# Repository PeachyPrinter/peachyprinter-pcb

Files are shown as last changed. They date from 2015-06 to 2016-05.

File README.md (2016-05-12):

If you're looking for the version of the Peachy Printer that we were gearing up to manufacture, look at mini-v1.14. 

If you're wondering what v1.15 is all about, it's a work-in-progress that we started because of a huge panic: right around the time we were getting ready for our final test manufacturing run, the STM32F042 practically vanished from the entire supply chain! We couldn't find them anywhere! So I quickly started redoing the board to use an STM32F070 instead, but in the end the supply chain recovered before we had to pull the trigger on the respin.

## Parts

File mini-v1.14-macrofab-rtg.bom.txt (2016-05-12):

Partlist exported from C:/Users/Tony/Dropbox/eagle/Peachy Pro/mini-v1.14-macrofab-rtg.sch at 2015-11-02 10:18 AM

Qty Value                Device                 Package           Parts                                                                    Description                                          MFG# MPN                           TEMP_COF TOLERANCE TP_SIGNAL_NAME VOLTAGE WATTAGE
4                        LEDCHIP-LED0603        CHIP-LED0603      LED1, LED2, LED3, LED4                                                   LED                                                                                                                                      
1                        PINHD-1X2              1X02              JP4                                                                      PIN HEADER                                                                                                                               
3                        PINHD-2X3              2X03              JP3, JP5, JP6                                                            PIN HEADER                                                                                                                               
1                        USB_MICRO_RIGHT        MICROUSB-RIGHT    J1                                                                       Library:  MF_Connectors                                                                                                                  
4   0.1uF                C-USC0603              C0603             C10, C11, C12, C13                                                       CAPACITOR, American symbol                                                                                                               
5   0.1uF                CAPACITOR_NP_0603      C0603             C8, C14, C16, C18, C20                                                   Library:  MF_Passives                                N/A                                N/A      N/A                      N/A            
2   10                   RESISTOR_0603          R0603             R16, R25                                                                 Library:  MF_Passives                                N/A                                         N/A                      N/A     N/A    
1   100k                 RESISTOR_0603          R0603             R4                                                                       Library:  MF_Passives                                N/A                                         N/A                      N/A     N/A    
4   100n                 CAPACITOR_NP_0603      C0603             C4, C5, C6, C7                                                           Library:  MF_Passives                                N/A                                N/A      N/A                      N/A            
1   10uF                 CAPACITOR_P_4MM        CP4MM             C3                                                                       Library:  MF_Passives                                N/A                                         N/A                      N/A            
2   13k3                 RESISTOR_0603          R0603             R1, R18                                                                  Library:  MF_Passives                                N/A                                         N/A                      N/A     N/A    
5   1k69                 RESISTOR_0603          R0603             R13, R14, R15, R38, R43                                                  Library:  MF_Passives                                N/A                                         N/A                      N/A     N/A    
2   1uF                  C-USC0603              C0603             C1, C2                                                                   CAPACITOR, American symbol                                                                                                               
3   1uF                  CAPACITOR_NP_0603      C0603             C9, C17, C19                                                             Library:  MF_Passives                                N/A                                N/A      N/A                      N/A            
16  2k                   RESISTOR_0603          R0603             R2, R3, R5, R7, R8, R9, R10, R20, R21, R22, R23, R27, R28, R29, R36, R37 Library:  MF_Passives                                N/A                                         N/A                      N/A     N/A    
1   560pF/50V            C-USC0603              C0603             C15                                                                      CAPACITOR, American symbol                                                                                                               
5   604k                 RESISTOR_0603          R0603             R24, R26, R32, R34, R41                                                  Library:  MF_Passives                                N/A                                         N/A                      N/A     N/A    
1   63k4                 RESISTOR_0603          R0603             R17                                                                      Library:  MF_Passives                                N/A                                         N/A                      N/A     N/A    
10  825k                 RESISTOR_0603          R0603             R6, R11, R12, R19, R30, R31, R33, R35, R39, R40                          Library:  MF_Passives                                N/A                                         N/A                      N/A     N/A    
1   BAT42                DIODE_SOD-123          SOD-123           D1                                                                       Library:  MF_Discrete_Semiconductor                  N/A                                                                                 
2   BSS138               N-CHANNEL_FET_SOT-23-3 SOT-23-3          U1, U3                                                                   Library:  MF_Discrete_Semiconductor                                                                                                      
1   GND                  TPB2,54                B2,54             TP2                                                                      Test pad                                                                                                                                 
4   LMC7101              LMC7101                SOT23-5           U$7, U$15, U$16, U$17                                                                                                                                                                                             
1   LMC7101              OPAMP-SINGLELMC7101    SOT23-5           U$5                                                                      Single amp opamps                                                                                                                        
1   LMR62014             LMR62014               SOT23-5           U$8                                                                                                                                                                                                               
1   MBR0520              MBR0520                SOD123            U$9                                                                                                                                                                                                               
1   N/C                  RESISTOR_0603          R0603             R42                                                                      Library:  MF_Passives                                N/A                                         N/A                      N/A     N/A    
2   NC7WZ14P6X           NC7WZ14P6X             SC70-6            U$2, U$4                                                                 2-circuit logic inverter, ultra-high-speed and cheap                                                                                     
1   SCOTT_LASERDIODELD3  SCOTT_LASERDIODELD3    SCOTT_LASERDIODE3 LD1                                                                                                                                3 x (0552-2-15-15-11-27-10-0)                                                  
1   SDR0403-100ML        SDR0403                SDR0403           U$14                                                                                                                                                                                                              
2   SMF6.0A              MBR0520                SOD123            U$10, U$13                                                                                                                                                                                                        
1   SP3002-04JTG         SP3002                 SC70-6            U$12                                                                                                                                                                                                              
1   STM32F042C6T6-LQFP48 STM32F042-LQFP48       LQFP48            U$1                                                                                                                                                                                                               
1   TLV70233PDBVR        TLV70233PDBVR          SOT-23-5          U2                                                                       Manufacturer Part #: TLV702                                                                                                              
10  TPB1,27              TPB1,27                B1,27             3V, GND, NRST, SWCLK, SWDIO, TP3, TP4, TP5, TP6, VUSB                    Test pad                                                                                                                                 
1   TPB2,54              TPB2,54                B2,54             LASER                                                                    Test pad                                                                                                                                 
1   ferrite              L-US                   C0603             L1                                                                       INDUCTOR, American symbol

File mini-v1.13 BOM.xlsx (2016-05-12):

Part | MF Part
2x3 Header | MF-CON-2.54mm-2x3 (https://beta.macrofab.net/project/9qdpte)
1u 0603 | MF-CAP-0603-1uF (https://beta.macrofab.net/part/MF-CAP-0603-1uF)
0.1u 0603 | MF-CAP-0603-0.1uF (https://beta.macrofab.net/part/MF-CAP-0603-0.1uF)
560pF | 399-1076-1-ND
ferrite | 445-1565-1-ND
LED | MF-LED-0603-RED
10u 4mm | MF-CAP-4MM-10uF (https://beta.macrofab.net/project/5xndt7)
2k | MF-RES-0603-2K (https://beta.macrofab.net/project/9qdpte/3)
825k | MF-RES-0603-825K (https://beta.macrofab.net/project/9qdpte/4)
1.69k | MF-RES-0603-1.69K (https://beta.macrofab.net/project/9qdpte/3)
63k4 | CRCW060363K4FKEA (https://beta.macrofab.net/project/9qdpte/3)
604k | MF-RES-0603-604K
13k3 | CRCW060313K3FKEA (https://beta.macrofab.net/project/9qdpte/3)
MBR0520 | MBR0520LCT-ND
mosfet | MF-DSC-SOT233-BSS138 (https://beta.macrofab.net/part/MF-DSC-SOT233-BSS138)
ldo | MF-SOT-235-3.3V-300mA (https://beta.macrofab.net/part/MF-SOT-235-3.3V-300mA)
lmc7101 | 576-2575-1-ND
lmr62014 | LMR62014XMF/NOPBCT-ND

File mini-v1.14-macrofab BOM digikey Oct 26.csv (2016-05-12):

Qty | Value | Device | DK P/N | Extended | DK for Ext$ | Package | DK Order Oct 26 | Boards Oct 26
13 | 100n | CAPACITOR_NP_0603 | 399-1095-2-ND | 65000 | 362.7 | C0603 | 4000 | 307
1 | 10uF | CAPACITOR_P_4MM | 490-7201-2-ND | 5000 | 484.35 | CP4MM | 250 | 250
5 | 1uF | C-USC0603 | 311-1443-2-ND | 25000 | 178.25 | C0603 | 4000 | 800
1 | 560pF/50V | C-USC0603 | 1276-1278-2-ND | 5000 | 62.9 | C0603 | 4000 | 4000
1 | BAT42 | DIODE_SOD-123 | BAT42W-FDITR-ND | 5000 | 442.2 | SOD-123 | 120 | 120
4 |  | LEDCHIP-LED0603 | 475-2512-2-ND | 20000 | 1071.2 | CHIP-LED0603 | 1000 | 250
5 | LMC7101 | LMC7101 | 576-2575-2-ND | 25000 | 7725.5 | SOT23-5 | 600 | 120
1 | LMR62014 | LMR62014 | 296-39046-2-ND | 5000 | 2595.55 | SOT23-5 | 120 | 120
1 | ferrite | L-US |  | 5000 |  | C0603 |  | 0
1 | MBR0520 | MBR0520 | MBR0520LT1GOSTR-ND | 5000 | 397.2 | SOD123 | 120 | 120
2 | SMF6.0A | MBR0520 | F5749TR-ND | 10000 | 1517.1 | SOD123 | 250 | 125
2 | NC7WZ14P6X | NC7WZ14P6X | NC7WZ14P6XTR-ND | 10000 | 810.4 | SC70-6 | 250 | 125
2 | BSS138 | N-CHANNEL_FET_SOT-23-3 | BSS138LT3GOSTR-ND | 10000 | 451.64 | SOT-23-3 | 240 | 120
3 |  | PINHD-2X3 | 952-1921-ND | 15000 | 2617.5 | 2X03 | 360 | 120
2 | 10 | RESISTOR_0603 | 311-10.0HRTR-ND | 10000 | 21.26 | R0603 | 5000 | 2500
1 | 100k | RESISTOR_0603 | 311-100KHRTR-ND | 5000 | 9.62 | R0603 | 5000 | 5000
2 | 13k3 | RESISTOR_0603 | 311-13.3KHRTR-ND | 10000 | 21.26 | R0603 | 5000 | 2500
5 | 1k69 | RESISTOR_0603 | 311-1.69KHRTR-ND | 25000 | 47.5 | R0603 | 5000 | 1000
16 | 2k | RESISTOR_0603 | 311-2.00KHRTR-ND | 80000 | 139.2 | R0603 | 5000 | 312
5 | 604k | RESISTOR_0603 | 311-604KHRTR-ND | 25000 | 47.5 | R0603 | 5000 | 1000
1 | 63k4 | RESISTOR_0603 | 311-63.4KHRTR-ND | 5000 | 12.45 | R0603 | 5000 | 5000
10 | 825k | RESISTOR_0603 | 311-825KHRTR-ND | 50000 | 21.62 | R0603 | 5000 | 500
1 | SDR0403-100ML | SDR0403 | SDR0403-100MLTR-ND | 5000 | 1287.25 | SDR0403 | 120 | 120
1 | SP3002-04JTG | SP3002 | F2916TR-ND | 5000 | 1824.75 | SC70-6 | 120 | 120
1 | STM32F070CBT6 | STM32F042-LQFP48 | 497-15099-ND | 5000 | 8179.93 | LQFP48 | 120 | 120
1 | TLV70233PDBVR | TLV70233PDBVR | 296-39284-2-ND | 5000 | 767.64 | SOT-23-5 | 120 | 120
1 |  | USB_MICRO_RIGHT | 609-4618-2-ND | 5000 | 1258.45 | MICROUSB-RIGHT | 120 | 120
TOTAL |  |  |  |  | 32354.92
PER BOARD |  |  |  |  | 6.470984

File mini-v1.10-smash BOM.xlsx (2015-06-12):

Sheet: mini-v1.10-smash
Qty | Total Qty | Value | Device | Package | Digikey Part
1 | 15 | 10uF | C-USC0603 | C0603 | 490-10475-1-ND |  | Number of Boards | 15
1 | 15 | 560pF/50V | C-USC0603 | C0603 | 399-1076-1-ND |  | Breakage | 0%
1 | 15 | 2.2u | C-USC0603 | C0603 | 587-2983-1-ND
1 | 15 | 10n | C-USC0603 | C0603 | 399-1091-1-ND
1 | 15 | 470p | C-USC0603 | C0603 | 399-1075-1-ND
1 | 15 | 820n | C-USC0603 | C0603 | 399-3117-1-ND
1 | 15 | 74S04D | 74S04D | SO14 | 568-1384-1-ND
1 | 15 | ferrite | L-US | C0603 | 445-1565-1-ND
1 | 15 | IRLR3105TR | FET-N-IRLR3105TRIRLR3105TR | DPAK | IRLR3105TRPBFCT-ND
1 | 15 | 10k | R-US_R0603 | R0603 | 541-10.0KHCT-ND
1 | 15 | 1 | R-US_R0603 | R0603 | 541-1.00HHCT-ND
1 | 15 | 100 | R-US_R0603 | R0603 | 541-100HCT-ND
1 | 15 | 9k9 | R-US_R0603 | R0603 | 541-9.09KHCT-ND
1 | 15 | 52k3 | R-US_R0603 | R0603 | 541-52.3KHCT-ND
1 | 15 | 13k3 | R-US_R0603 | R0603 | 541-13.3KHCT-ND
1 | 15 | 100k | R-US_R0603 | R0603 | 541-100KHCT-ND
1 | 15 | LD3985M33R | LD3985MXXR | SOT23-5L | LP3985IM5-3.3/NOPBCT-ND
1 | 15 | STM32F042-LQFP48 | STM32F042-LQFP48 | LQFP48 | 497-14648-ND
1 | 15 | SDR0403-100ML | SDR0403 | SDR0403 | SDR0403-100MLCT-ND
1 | 15 | FCI-MICRO-USB | FCI-MICRO-USB | FCI-MICROUSB | 609-4613-1-ND
1 | 15 | LMR62014 | LMR62014 | SOT23-5 | LMR62014XMF/NOPBCT-ND
1 | 15 | MBR0520 | MBR0520 | SOD123 | MBR0520LCT-ND
1 | 15 | LMH6645MF | OPAMP-SINGLELMH6645MF | SOT23-5 | LMH6645MF/NOPBCT-ND
2 | 30 | BAT60A | BAT60A | SOD323 | BAT60AE6327INCT-ND
2 | 30 | SMF6.0A | MBR0520 | SOD123 | F5749CT-ND
2 | 30 | SP3002 | SP3002 | SC70-6 | F2916CT-ND | Substituted
3 | 45 | 1u | C-USC0603 | C0603 | 587-1242-1-ND
4 | 60 | 470n | C-USC0603 | C0603 | 587-1252-1-ND
4 | 60 | 4.7n | C-USC0603 | C0603 | 399-1087-1-ND
4 | 60 |  | LEDCHIP-LED0603 | CHIP-LED0603 | 475-2512-1-ND
4 | 60 | LMC7101 | LMC7101 | SOT23-5 | 576-2575-1-ND
5 | 75 | 100n | C-USC0603 | C0603 | 399-1095-1-ND
5 | 75 | 1M | R-US_R0603 | R0603 | 541-1.00MHCT-ND
6 | 90 | 1k | R-US_R0603 | R0603 | 541-1.00KHCT-ND
12 | 180 | 1k96 | R-US_R0603 | R0603 | 541-1.96KHCT-ND

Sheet: Digikey Kitting
#Kits | Cost | Cost/Board
1 | 40 | 40
15 | 338.33 | 22.55533333
20 | 440 | 22
1000 | 10118.43 | 10.11843
2500 | 27284.62 | 10.913848
5000 | 47519.85 | 9.50397

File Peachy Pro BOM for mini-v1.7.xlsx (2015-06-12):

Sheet: Ordering
Value | Device | Package | Digikey Part | Newark Part Number | Unit Price | /1000 price | QTY | Single Price | Vol Price | QTY +15%
100n | C-USC0603 | C0603 | 399-1095-1-ND |  | 0.13 | 0.00816 | 5 | 0.65 | 0.0408 | 58
10n | C-USC0603 | C0603 | 399-8988-1-ND |  | 0.32 | 0.06934 | 1 | 0.32 | 0.06934 | 12
10uF | C-USC0603 | C0603 | 490-10475-1-ND |  | 0.27 | 0.05056 | 1 | 0.27 | 0.05056 | 12
1u | C-USC0603 | C0603 | 587-1242-1-ND |  | 0.13 | 0.01321 | 3 | 0.39 | 0.03963 | 35
2.2u | C-USC0603 | C0603 | 587-2983-1-ND |  | 0.22 | 0.04095 | 1 | 0.22 | 0.04095 | 12
4.7n | C-USC0603 | C0603 | 399-1087-1-ND |  | 0.13 | 0.00971 | 4 | 0.52 | 0.03884 | 46
470n | C-USC0603 | C0603 | 587-1252-1-ND |  | 0.13 | 0.02136 | 4 | 0.52 | 0.08544 | 46
470p | C-USC0603 | C0603 | 399-1075-1-ND |  | 0.13 | 0.01398 | 1 | 0.13 | 0.01398 | 12
560pF/50V | C-USC0603 | C0603 | 399-1076-1-ND |  | 0.32 | 0.07911 | 1 | 0.32 | 0.07911 | 12
820n | C-USC0603 | C0603 | 399-3117-1-ND |  | 0.34 | 0.08216 | 1 | 0.34 | 0.08216 | 12
BAT60A | BAT60A | SOD323 | BAT60AE6327INCT-ND |  | 0.71 | 0.14888 | 2 | 1.42 | 0.29776 | 23
74S04D | 74S04D | SO14 | 568-1384-1-ND |  | 0.63 | 0.13336 | 1 | 0.63 | 0.13336 | 12
 | LEDCHIP-LED0603 | CHIP-LED0603 | 475-2512-1-ND |  | 0.12 | 0.06086 | 4 | 0.48 | 0.24344 | 46
IRLR3105TR | FET-N-IRLR3105TRIRLR3105TR | DPAK | IRLR3105TRPBFCT-ND |  | 1.48 | 0.5535 | 1 | 1.48 | 0.5535 | 12
1 | R-US_R0603 | R0603 | 541-1.00HHCT-ND |  | 0.112 | 0.02359 | 1 | 0.112 | 0.02359 | 12
100 | R-US_R0603 | R0603 | 541-100HCT-ND |  | 0.112 | 0.02359 | 1 | 0.112 | 0.02359 | 12
100k | R-US_R0603 | R0603 | 541-100KHCT-ND |  | 0.112 | 0.02359 | 1 | 0.112 | 0.02359 | 12
10k | R-US_R0603 | R0603 | 541-10.0KHCT-ND |  | 0.112 | 0.02359 | 1 | 0.112 | 0.02359 | 12
13k3 | R-US_R0603 | R0603 | 541-13.3KHCT-ND |  | 0.112 | 0.02359 | 1 | 0.112 | 0.02359 | 12
1k | R-US_R0603 | R0603 | 541-1.00KHCT-ND |  | 0.112 | 0.02359 | 2 | 0.224 | 0.04718 | 23
1M | R-US_R0603 | R0603 | 541-1.00MHCT-ND |  | 0.112 | 0.02359 | 5 | 0.56 | 0.11795 | 58
3k9 | R-US_R0603 | R0603 | 541-3.90KHCT-ND |  | 0.112 | 0.02359 | 4 | 0.448 | 0.09436 | 46
52k3 | R-US_R0603 | R0603 | 541-52.3KHCT-ND |  | 0.112 | 0.02359 | 1 | 0.112 | 0.02359 | 12
9k9 | R-US_R0603 | R0603 | 541-9.09KHCT-N |  | 0.112 | 0.02359 | 1 | 0.112 | 0.02359 | 12
LD3985M33R | LD3985MXXR | SOT23-5L | 497-3504-1-ND |  | 0.96 | 0.33535 | 1 | 0.96 | 0.33535 | 12
 | R-US_R0603 | R0603 | 541-1.00KHCT-ND |  | 0.112 | 0.02359 | 4 | 0.448 | 0.09436 | 46
FCI-MICRO-USB | FCI-MICRO-USB | FCI-MICROUSB | 609-4613-1-ND |  | 0.6 | 0.3365 | 1 | 0.6 | 0.3365 | 12
LMC7101 | LMC7101 | SOT23-5 | 576-2575-1-ND |  | 0.98 | 0.389 | 4 | 3.92 | 1.556 | 46
LMH6645MF | OPAMP-SINGLELMH6645MF | SOT23-5 | LMH6645MF/NOPBCT-ND |  | 2.49 | 0.97596 | 1 | 2.49 | 0.97596 | 12
LMR62014 | LMR62014 | SOT23-5 | LMR62014XMF/NOPBCT-ND |  | 2.32 | 0.80116 | 1 | 2.32 | 0.80116 | 12
MBR0520 | MBR0520 | SOD123 | MBR0520LT1GOSCT-ND | 48K7498 | 0.407 | 0.076 | 3 | 1.221 | 0.228 | 35
SDR0403-100ML | SDR0403 | SDR0403 | SDR0403-100MLCT-ND |  | 0.65 | 0.31547 | 1 | 0.65 | 0.31547 | 12
SP3002 | SP3002 | SC70-6 | F2916CT-ND |  | 0.96 | 0.38456 | 2 | 1.92 | 0.76912 | 23
STM32F042-LQFP48 | STM32F042-LQFP48 | LQFP48 | 497-14648-ND |  | 4.08 | 2.04112 | 1 | 4.08 | 2.04112 | 12
 | L_TDK_1005 | MLK1005 | 445-1565-1-ND |  | 0.13 | 0.03518 | 1 | 0.13 | 0.03518 | 12
 | NOTE: Replace the existing one with this one (0603)
 |  |  |  |  |  |  | 68 | 28.445 | 9.68171

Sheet: Assembly
Value | QTY | x3
100n | 5 | 15
10n | 1 | 3
10uF | 1 | 3
1u | 3 | 9
2.2u | 1 | 3
4.7n | 4 | 12
470n | 4 | 12
470p | 1 | 3
560pF/50V | 1 | 3
820n | 1 | 3
BAT60A | 2 | 6
74S04D | 1 | 3
 | 4 | 12
IRLR3105TR | 1 | 3
1 | 1 | 3
100 | 1 | 3
100k | 1 | 3
10k | 1 | 3
13k3 | 1 | 3
1k | 2 | 6
1M | 5 | 15
3k9 | 4 | 12
52k3 | 1 | 3
9k9 | 1 | 3
LD3985M33R | 1 | 3
 | 4 | 12
FCI-MICRO-USB | 1 | 3
LMC7101 | 4 | 12
LMH6645MF | 1 | 3
LMR62014 | 1 | 3
MBR0520 | 3 | 9
SDR0403-100ML | 1 | 3
SP3002 | 2 | 6
STM32F042-LQFP48 | 1 | 3
 | 1
 | 68

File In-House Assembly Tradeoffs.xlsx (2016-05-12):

Item | Cost ($USD) | Cost ($CAD) | Assumptions/Notes
Pick and Place Machine |  | $17415.00 | Probably need extra feeders (DP2006-3)
Labour |  | $4933.33 | 1hr per batch labour, 75 boards per batch, $20/hr + 1 week setup time @ $90/hr
Components |  | $32354.92
PCB Manufacture |  | 5148.60 | RFQ from goldphoenix for 5000 boards, 11 day lead
Total |  | $59851.85
Components | $27850.00 | $37597.50 | 1.35 exchange rate
PCBs | $2150.00 | $2902.50
Labour | $13400.00 | $18090.00
Total |  | $58590.00 | or $60,702 to do it in 2 batches of 2500

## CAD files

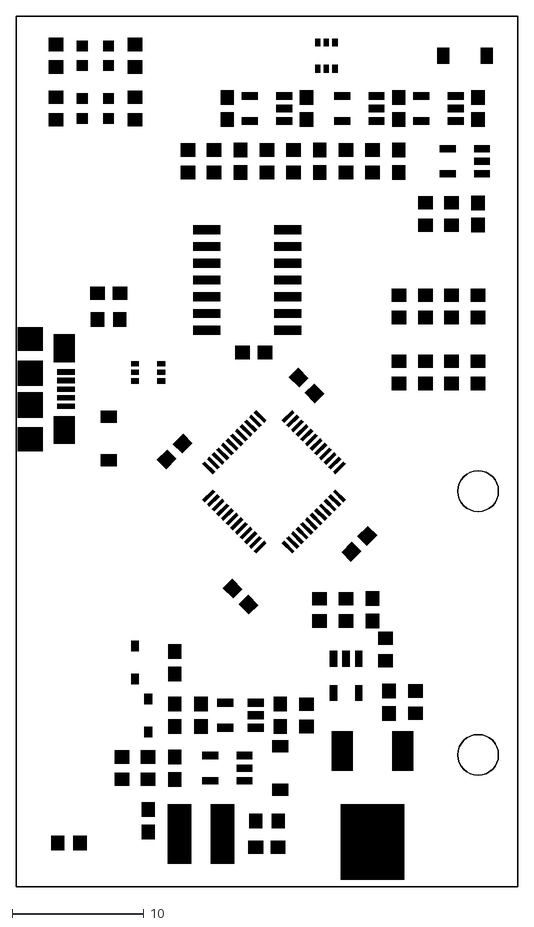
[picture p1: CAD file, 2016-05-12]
mini-v1.10-smash-4.dxf
38.0 x 66.0

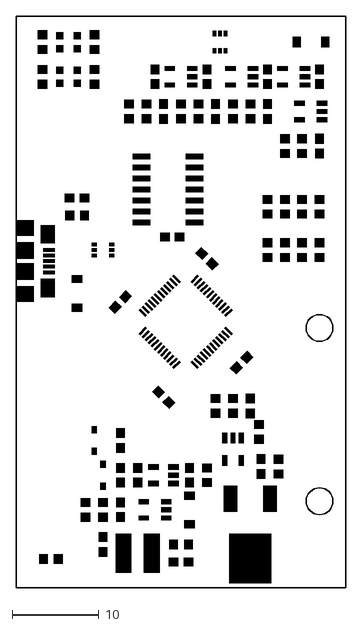
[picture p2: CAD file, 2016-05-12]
mini-v1.10-smash-3.dxf
38.0 x 66.0

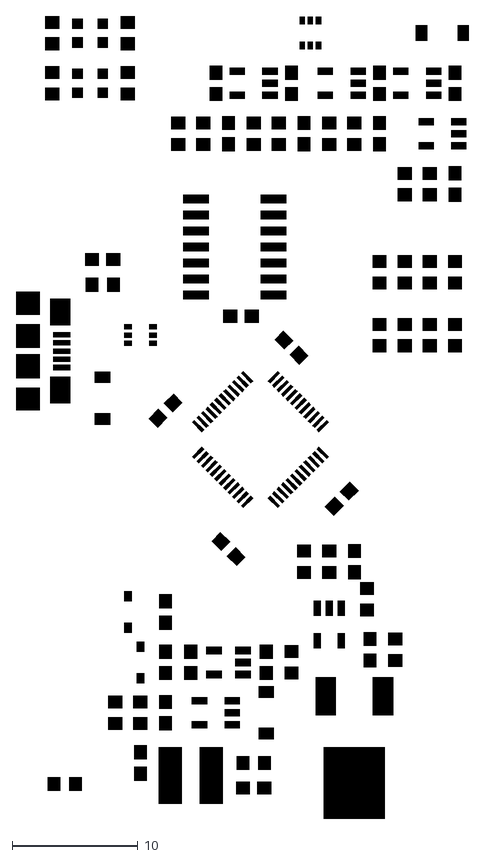
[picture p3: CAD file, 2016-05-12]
mini-v1.10-smash-7.dxf
36.0 x 63.8

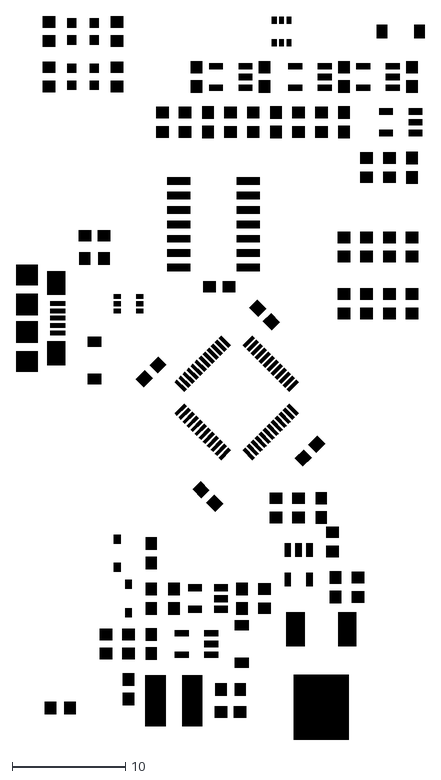
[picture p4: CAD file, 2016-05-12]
mini-v1.10-smash-10.dxf
36.0 x 63.8

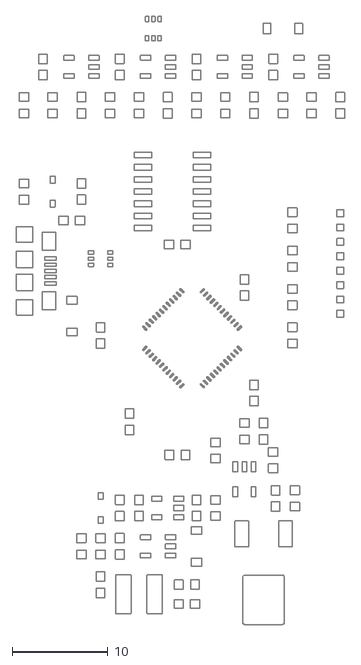
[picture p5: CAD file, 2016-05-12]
mini-v1.7-bigger-tcream-tweaked.dxf
34.2 x 63.4

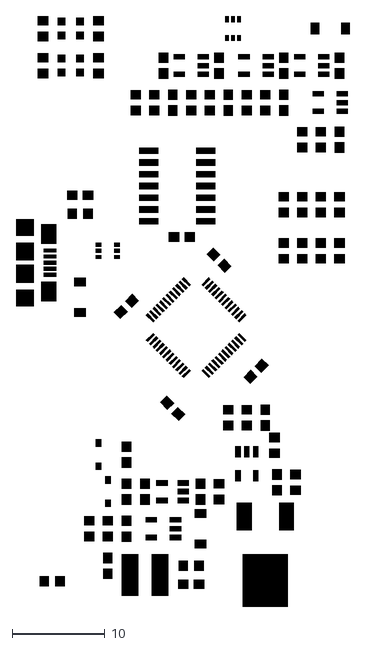
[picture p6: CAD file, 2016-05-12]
mini-v1.10-smash-6.dxf
36.0 x 63.8

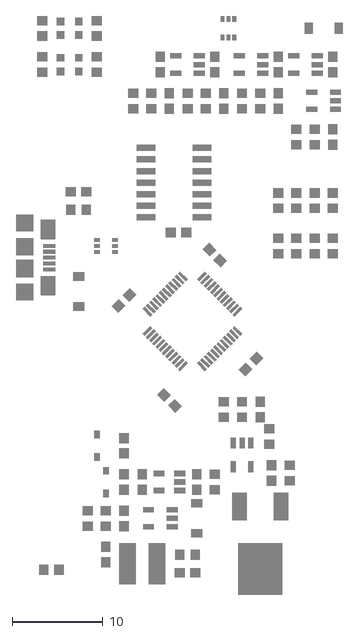
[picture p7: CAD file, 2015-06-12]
mini-v1.10-smash-8.dxf
36.0 x 63.8

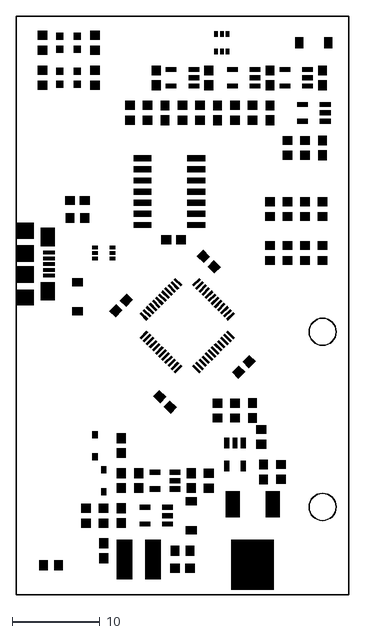
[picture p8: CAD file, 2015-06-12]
mini-v1.10-smash-2.dxf
38.0 x 66.0

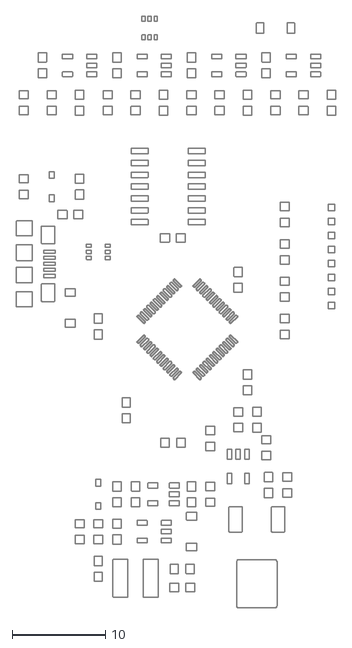
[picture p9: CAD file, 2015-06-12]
mini-v1.7-bigger-tcream.dxf
34.2 x 63.4

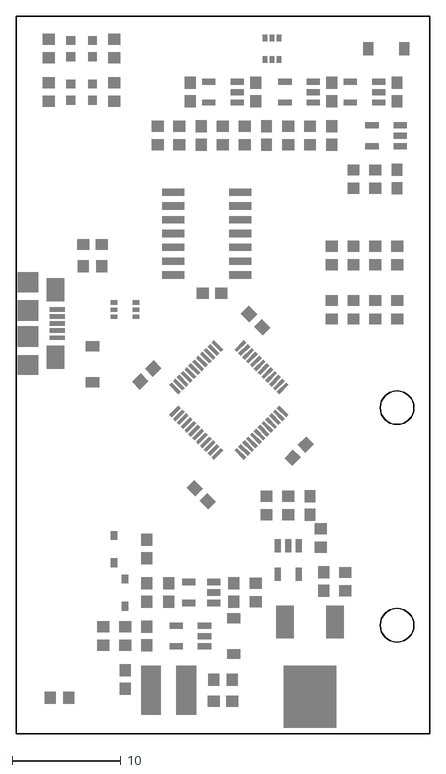
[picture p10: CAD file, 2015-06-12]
mini-v1.10-smash-5.dxf
38.0 x 66.0

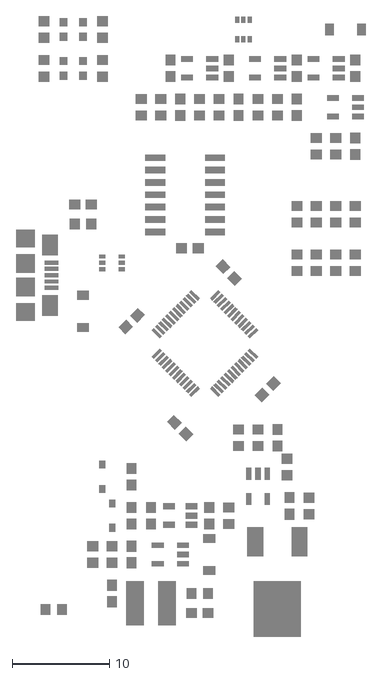
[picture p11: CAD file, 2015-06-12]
mini-v1.10-smash-9.dxf
36.0 x 63.8

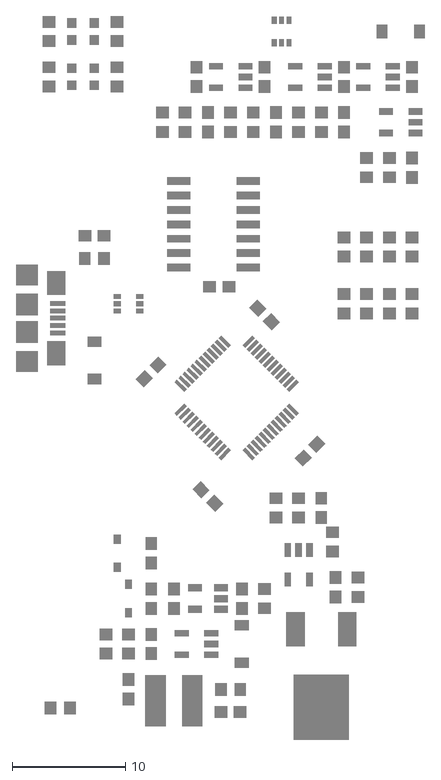
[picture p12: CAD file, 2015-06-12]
mini-v1.10-smash-7.1.dxf
36.0 x 63.8

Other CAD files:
mini-v1.10-smash-bcream.dxf
mini-v1.10-smash-tcream.dxf
mini-v1.10-smash-10.dwg
mini-v1.10-smash.dwg

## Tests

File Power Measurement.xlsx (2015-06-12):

Power Setting | Approx Current (mA) | Raw Measurement uW | Corrected mW | Raw w/o aperature mW | mW w/o aperature | aperature % | Raw w/o aperature, bigger dot | mW w/o aperature, bigger | Big dot/small
12 | 15.52941176 |  |  |  |  |  | 0.00361 | 0.035017 |  | Note: this was all done with a 10:1 current setting ratio. Iout = 3.3V * 1/10 (A/V) * x / 255 This is both dangerous and inefficient. We're going to change the ratio s.t. ~25mW output power is represented by 255. This would have been on v1.7 of the circuit
15 | 19.41176471 |  |  |  |  |  | 0.00467 | 0.045299
19 | 24.58823529 |  |  |  |  |  | 0.00682 | 0.066154
20 | 25.88235294 |  |  |  |  |  | 0.00768 | 0.074496
25 | 32.35294118 |  |  | 0.085 | 0.8245 |  | 0.104 | 1.0088 | 1.223529412
30 | 38.82352941 | 78.5 | 0.76145 | 0.695 | 6.7415 | 0.1129496403 | 0.755 | 7.3235 | 1.086330935
32 | 41.41176471 | 101.6 | 0.98552 | 1.024 | 9.9328 | 0.09921875 | 1.031 | 10.0007 | 1.006835938
34 | 44 | 125.1 | 1.21347 | 1.285 | 12.4645 | 0.0973540856 | 1.306 | 12.6682 | 1.016342412
36 | 46.58823529 | 145.2 | 1.40844 | 1.541 | 14.9477 | 0.09422452953 | 1.582 | 15.3454 | 1.0266061
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

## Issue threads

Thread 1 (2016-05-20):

Missing components model codes on

luckcolors, 2016-05-20:
Hello.
I was looking at the mini-v1.14-macrofab-rtg.sch and some components names are missing(i mean the part code ):
-laser
-motor

Also it would be great if you could provide description (or name) of what goes on the following pins:

Schematic sheet 2:
-TP3
-TP4
-TP5
-TP6

Schematic sheet 3:
-TP2

Schematic sheet 4:
-3V  VUSB
-SWCLK  NRST
-SWDIO GND
Thanks in advance. :+1:

tonyarkles, 2016-05-20:
TPs are test points. 3V is the 3V rail, VUSB is the USB rail.
SWCLK/SWDIO/NRST/GND are the standard ARM Cortex-M SWD debugging
connections (similar to JTAG, but fewer wires).

No parts to be mounted for any of these.

On Fri, May 20, 2016 at 1:15 PM, luckcolors <notifications@github.com>
wrote:

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

luckcolors, 2016-05-20:
Ok thanks @tonyarkles.
Then the only thing that's really missing is the motor and laser component code.

tonyarkles, 2016-05-21:
Motor? There is no motor... Are you looking at the ferrite bead maybe?

I have no clue what the laser part number is. @Rylan?

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

luckcolors, 2016-05-21:
Ah yeah. Sorry it hough there was a motor there. :P
So then what's really missing is the laser.

luckcolors, 2016-05-21:
Also resistance value for R42 is missing.

tonyarkles, 2016-05-21:
I'm doing some yard work, but if I recall R42 was an escape hatch in case the modification between v1.13 and v1.14 didn't work. I think it's a no-place but I'll double check when I'm back inside.

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

luckcolors, 2016-05-23:
so any idea on the laser?
For sure it's ultraviolet but with what potency and Voltage would it be?

luckcolors, 2016-05-24:
The only thing i found in the sch file is the value attached to the LD1 component.
mpn 3 x (0552-2-15-15-11-27-10-0)
Which appears to be this: [http://www.digikey.com/product-detail/en/mill-max-manufacturing-corp/0552-2-15-15-11-27-10-0/ED90096-ND/947104](link).
It's a pin socket.....

tonyarkles, 2016-05-24:
Totally a placeholder. That's a carry-over from the original analog board.
We were using a socket on the boards, and then a laser diode, but I wasn't
responsible for those as far as I recall.

In general, any UV laser diode will work, so long as Vf <= around 6V, and
If is less than about 200mA. The circuit is pretty robust against different
diode parameters. It's a constant current driver, so you tell it (through
the firmware) how much current you want to go through the diode, and it
adjusts everything to make sure that much current is running through the
laser.

On Tue, May 24, 2016 at 3:41 PM, luckcolors <notifications@github.com>
wrote:

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

luckcolors, 2016-05-25:
Ok. So one last detail: must the laser light wavelenght be atleast less than 380nm(ultrviolet light boundary) or it can be more (like 405nm which is violet light check wikipedia ultraviolet for more info).

tonyarkles, 2016-05-25:
I'm pretty sure 405 is A-OK.

The socket was an LD254-3P-24 from jccherry.com.
http://jccherry.com/products/Laser_Diode_Sockets/Laser_Diode_Socket_2.54mm_pitch.pdf#view=fitV,
100

You don't *have* to use a socket, but the laser diodes are pretty sensitive
and tricky to solder without cooking it. I'm pretty sure but not 100% sure
that these sockets will work too if jccherry doesn't want to sell one-offs:
http://www.aixiz.com/store/product_info.php/cPath/70/products_id/454/osCsid/c2d8dafd1f5eaab5671f0e8ee4d64784

You can probably also find an appropriate diode from aixiz

On Wed, May 25, 2016 at 3:05 AM, luckcolors <notifications@github.com>
wrote:

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

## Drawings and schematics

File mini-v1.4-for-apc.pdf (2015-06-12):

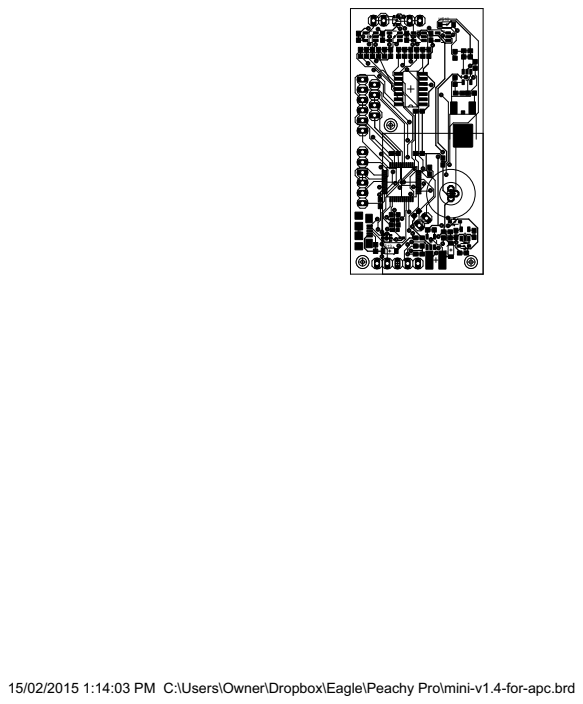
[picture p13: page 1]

15/02/2015 1:14:03 PM C:\Users\Owner\Dropbox\Eagle\Peachy Pro\mini-v1.4-for-apc.brd

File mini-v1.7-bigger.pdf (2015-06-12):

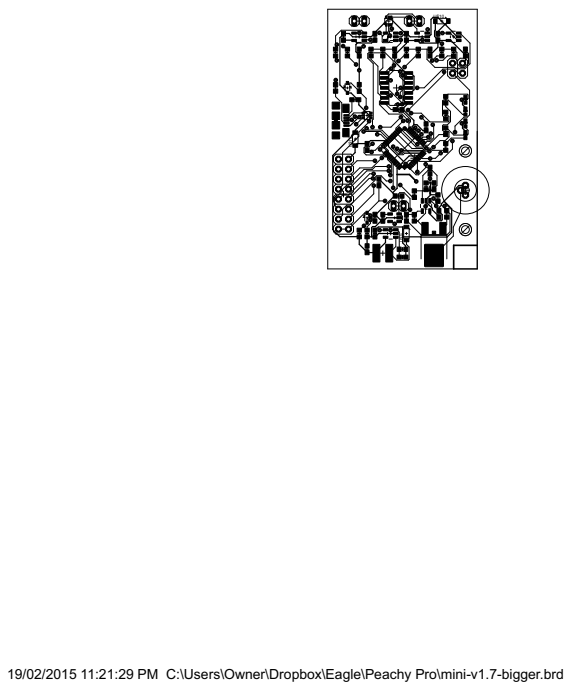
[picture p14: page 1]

19/02/2015 11:21:29 PM C:\Users\Owner\Dropbox\Eagle\Peachy Pro\mini-v1.7-bigger.brd

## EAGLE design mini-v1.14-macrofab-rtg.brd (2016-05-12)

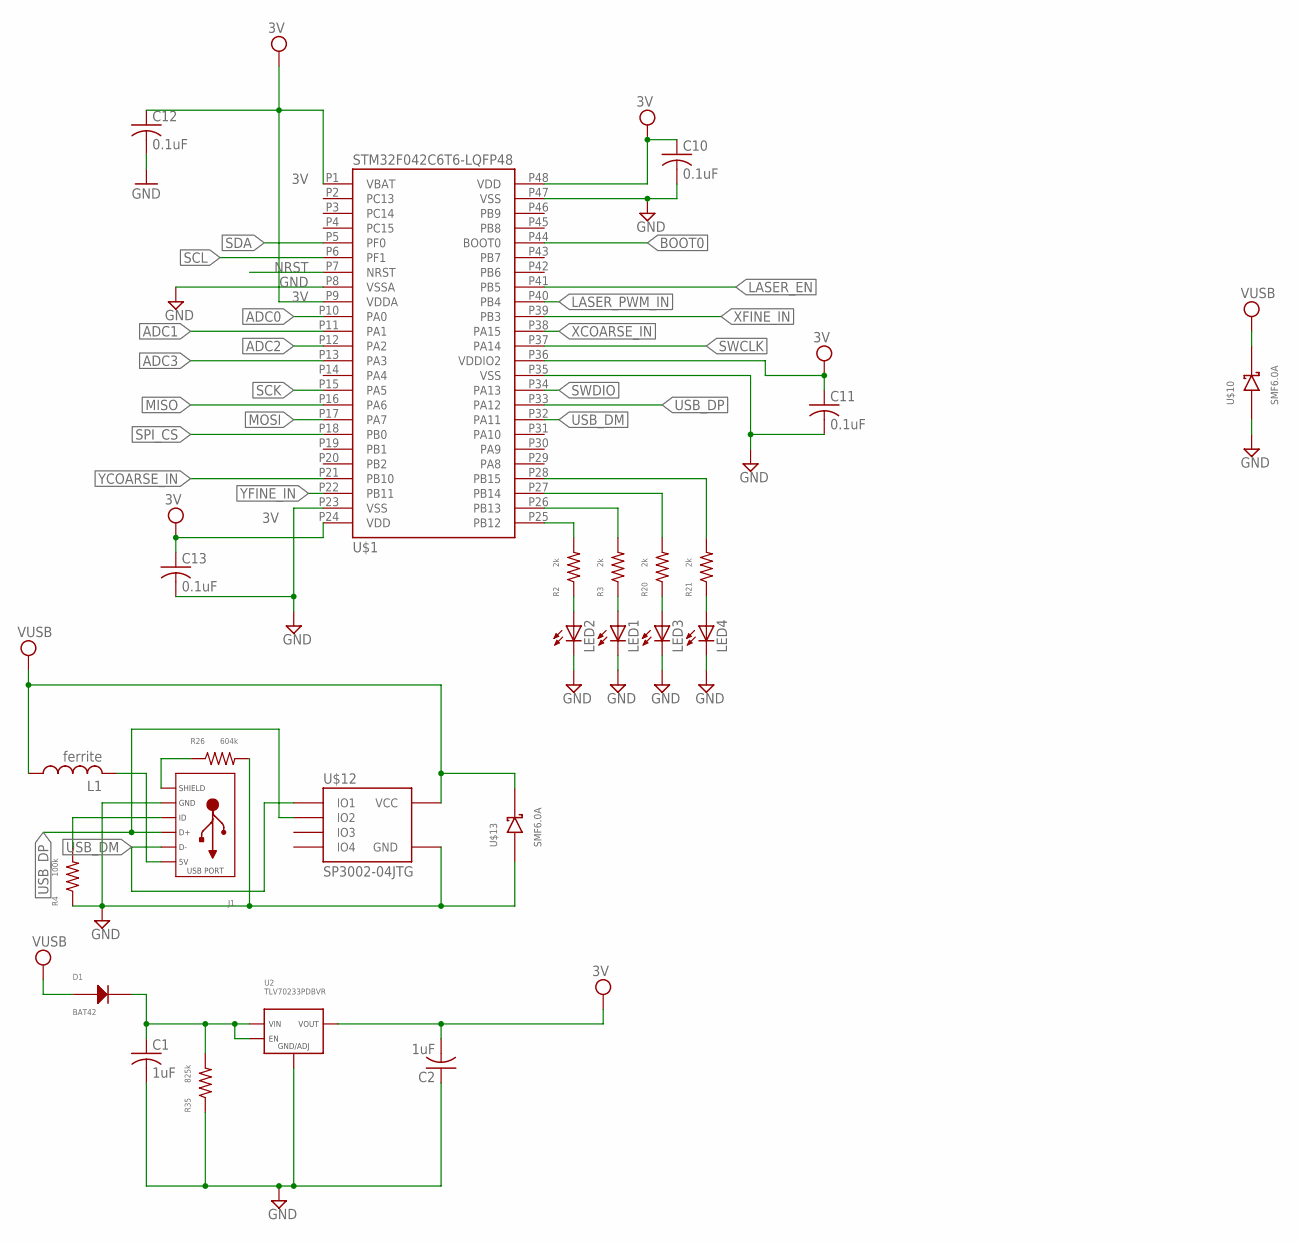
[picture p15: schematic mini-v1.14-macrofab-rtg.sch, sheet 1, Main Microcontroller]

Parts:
C1, C2: 1uF; C0603
C10, C11, C12, C13: 0.1uF; C0603
D1: BAT42; SOD-123
J1: USB_MICRO_RIGHT; MICROUSB-RIGHT
L1: ferrite; C0603
LED1, LED2, LED3, LED4: LEDCHIP-LED0603; CHIP-LED0603
R2, R3, R20, R21: 2k; R0603
R4: 100k; R0603
R26: 604k; R0603
R35: 825k; R0603
U2: TLV70233PDBVR; SOT-23-5
U$1: STM32F042C6T6-LQFP48; LQFP48
U$10, U$13: SMF6.0A; SOD123
U$12: SP3002-04JTG; SC70-6

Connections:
3V: C2.2, C10.1, C11.1, C12.1, C13.1, U2.P$5 (VOUT), U$1.P1 (VBAT), U$1.P9 (VDDA), U$1.P24 (VDD), U$1.P36 (VDDIO2), U$1.P48 (VDD); also elsewhere on the board
ADC0: U$1.P10 (PA0); also elsewhere on the board
ADC1: U$1.P11 (PA1); also elsewhere on the board
ADC2: U$1.P12 (PA2); also elsewhere on the board
ADC3: U$1.P13 (PA3); also elsewhere on the board
BOOT0: U$1.P44 (BOOT0); also elsewhere on the board
GND: C1.2, C2.1, C10.2, C11.2, C12.2, C13.2, J1.5 (GND), LED1.C, LED2.C, LED3.C, LED4.C, R4.P$1, R26.P$2, R35.P$1, U2.P$2 (GND/ADJ), U$1.P8 (VSSA), U$1.P23 (VSS), U$1.P35 (VSS), U$1.P47 (VSS), U$10.ANODE, U$12.P2 (GND), U$13.ANODE; also elsewhere on the board
LASER_EN: U$1.P41 (PB5); also elsewhere on the board
LASER_PWM_IN: U$1.P40 (PB4); also elsewhere on the board
MISO: U$1.P16 (PA6); also elsewhere on the board
MOSI: U$1.P17 (PA7); also elsewhere on the board
unnamed: R2.P$2, U$1.P25 (PB12)
unnamed: LED2.A, R2.P$1
unnamed: C1.1, D1.CATHODE, R35.P$2, U2.P$1 (VIN), U2.P$3 (EN)
unnamed: J1.4 (ID), R4.P$2
unnamed: LED1.A, R3.P$1
unnamed: R3.P$2, U$1.P26 (PB13)
unnamed: J1.1 (5V), L1.2
unnamed: J1.S1 (SLD), J1.S2 (SLD), J1.S3 (SLD), J1.S4 (SLD), J1.S5 (SLD), J1.S6 (SLD), R26.P$1
unnamed: LED3.A, R20.P$1
unnamed: LED4.A, R21.P$1
unnamed: R20.P$2, U$1.P27 (PB14)
unnamed: R21.P$2, U$1.P28 (PB15)
NRST: U$1.P7 (NRST); also elsewhere on the board
SCK: U$1.P15 (PA5); also elsewhere on the board
SCL: U$1.P6 (PF1); also elsewhere on the board
SDA: U$1.P5 (PF0); also elsewhere on the board
SPI_CS: U$1.P18 (PB0); also elsewhere on the board
SWCLK: U$1.P37 (PA14); also elsewhere on the board
SWDIO: U$1.P34 (PA13); also elsewhere on the board
USB_DM: J1.2 (D-), U$1.P32 (PA11), U$12.P1 (IO1)
USB_DP: J1.3 (D+), U$1.P33 (PA12), U$12.P3 (IO2)
VUSB: D1.ANODE, L1.1, U$10.CATHODE, U$12.P5 (VCC), U$13.CATHODE; also elsewhere on the board
XCOARSE_IN: U$1.P38 (PA15); also elsewhere on the board
XFINE_IN: U$1.P39 (PB3); also elsewhere on the board
YCOARSE_IN: U$1.P21 (PB10); also elsewhere on the board
YFINE_IN: U$1.P22 (PB11); also elsewhere on the board

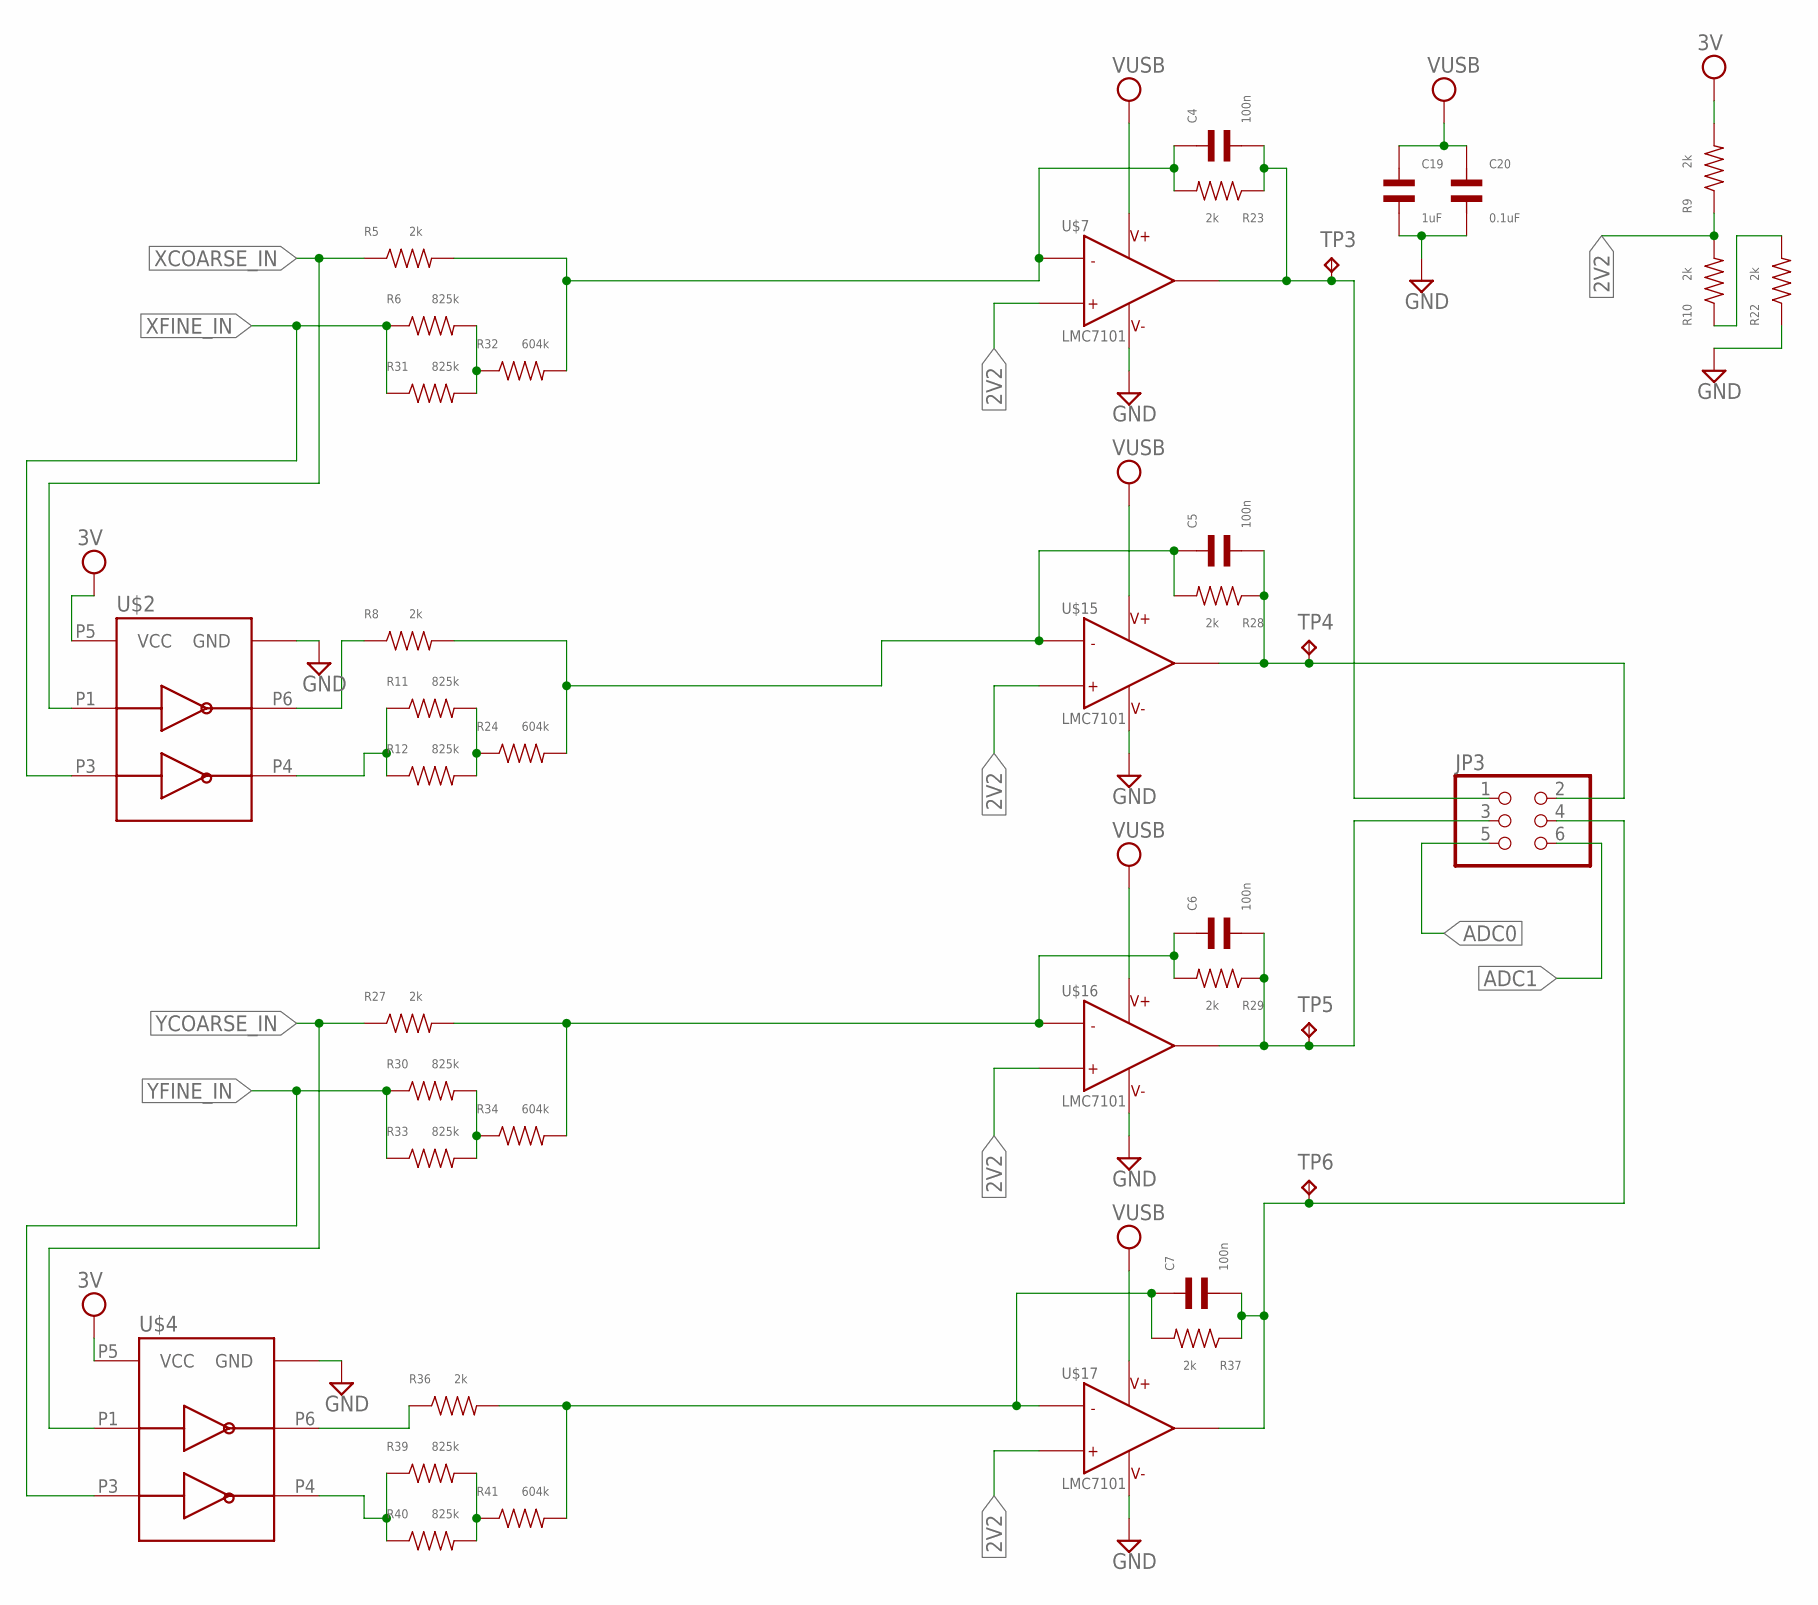
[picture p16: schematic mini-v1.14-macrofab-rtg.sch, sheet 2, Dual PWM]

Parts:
C4, C5, C6, C7: 100n; C0603
C19: 1uF; C0603
C20: 0.1uF; C0603
JP3: PINHD-2X3; 2X03
R5, R8, R9, R10, R22, R23, R27, R28, R29, R36, R37: 2k; R0603
R6, R11, R12, R30, R31, R33, R39, R40: 825k; R0603
R24, R32, R34, R41: 604k; R0603
TP3, TP4, TP5, TP6: TPB1,27; B1,27
U$2, U$4: NC7WZ14P6X; SC70-6
U$7, U$15, U$16, U$17: LMC7101; SOT23-5

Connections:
2V2: R9.P$1, R10.P$2, U$7.3, U$15.3, U$16.3, U$17.3
3V: R9.P$2, U$2.P5 (VCC), U$4.P5 (VCC); also elsewhere on the board
ADC0: JP3.5; also elsewhere on the board
ADC1: JP3.6; also elsewhere on the board
COARSE1: R8.P$1, U$2.P6 (Y1)
FINE1: R11.P$1, R12.P$1, U$2.P4 (Y2)
FINE3: R39.P$1, R40.P$1, U$4.P4 (Y2)
GND: C19.P$2, C20.P$2, R22.P$1, U$2.P2 (GND), U$4.P2 (GND), U$7.5, U$15.5, U$16.5, U$17.5; also elsewhere on the board
unnamed: R36.P$1, U$4.P6 (Y1)
unnamed: R11.P$2, R12.P$2, R24.P$1
unnamed: C5.P$1, R8.P$2, R24.P$2, R28.P$2, U$15.4
unnamed: R10.P$1, R22.P$2
unnamed: R30.P$2, R33.P$2, R34.P$1
unnamed: R6.P$2, R31.P$2, R32.P$1
unnamed: C6.P$1, R27.P$2, R29.P$2, R34.P$2, U$16.4
unnamed: R39.P$2, R40.P$2, R41.P$1
unnamed: C7.P$1, R36.P$2, R37.P$2, R41.P$2, U$17.4
OUT: C4.P$2, JP3.1, R23.P$1, TP3.TP, U$7.1
OUT1: C5.P$2, JP3.2, R28.P$1, TP4.TP, U$15.1
OUT2: C6.P$2, JP3.3, R29.P$1, TP5.TP, U$16.1
OUT3: C7.P$2, JP3.4, R37.P$1, TP6.TP, U$17.1
VUSB: C19.P$1, C20.P$1, U$7.2, U$15.2, U$16.2, U$17.2; also elsewhere on the board
XCOARSE_IN: R5.P$1, U$2.P1 (A1); also elsewhere on the board
XFINE_IN: R6.P$1, R31.P$1, U$2.P3 (A2); also elsewhere on the board
XSUM: C4.P$1, R5.P$2, R23.P$2, R32.P$2, U$7.4
YCOARSE_IN: R27.P$1, U$4.P1 (A1); also elsewhere on the board
YFINE_IN: R30.P$1, R33.P$1, U$4.P3 (A2); also elsewhere on the board

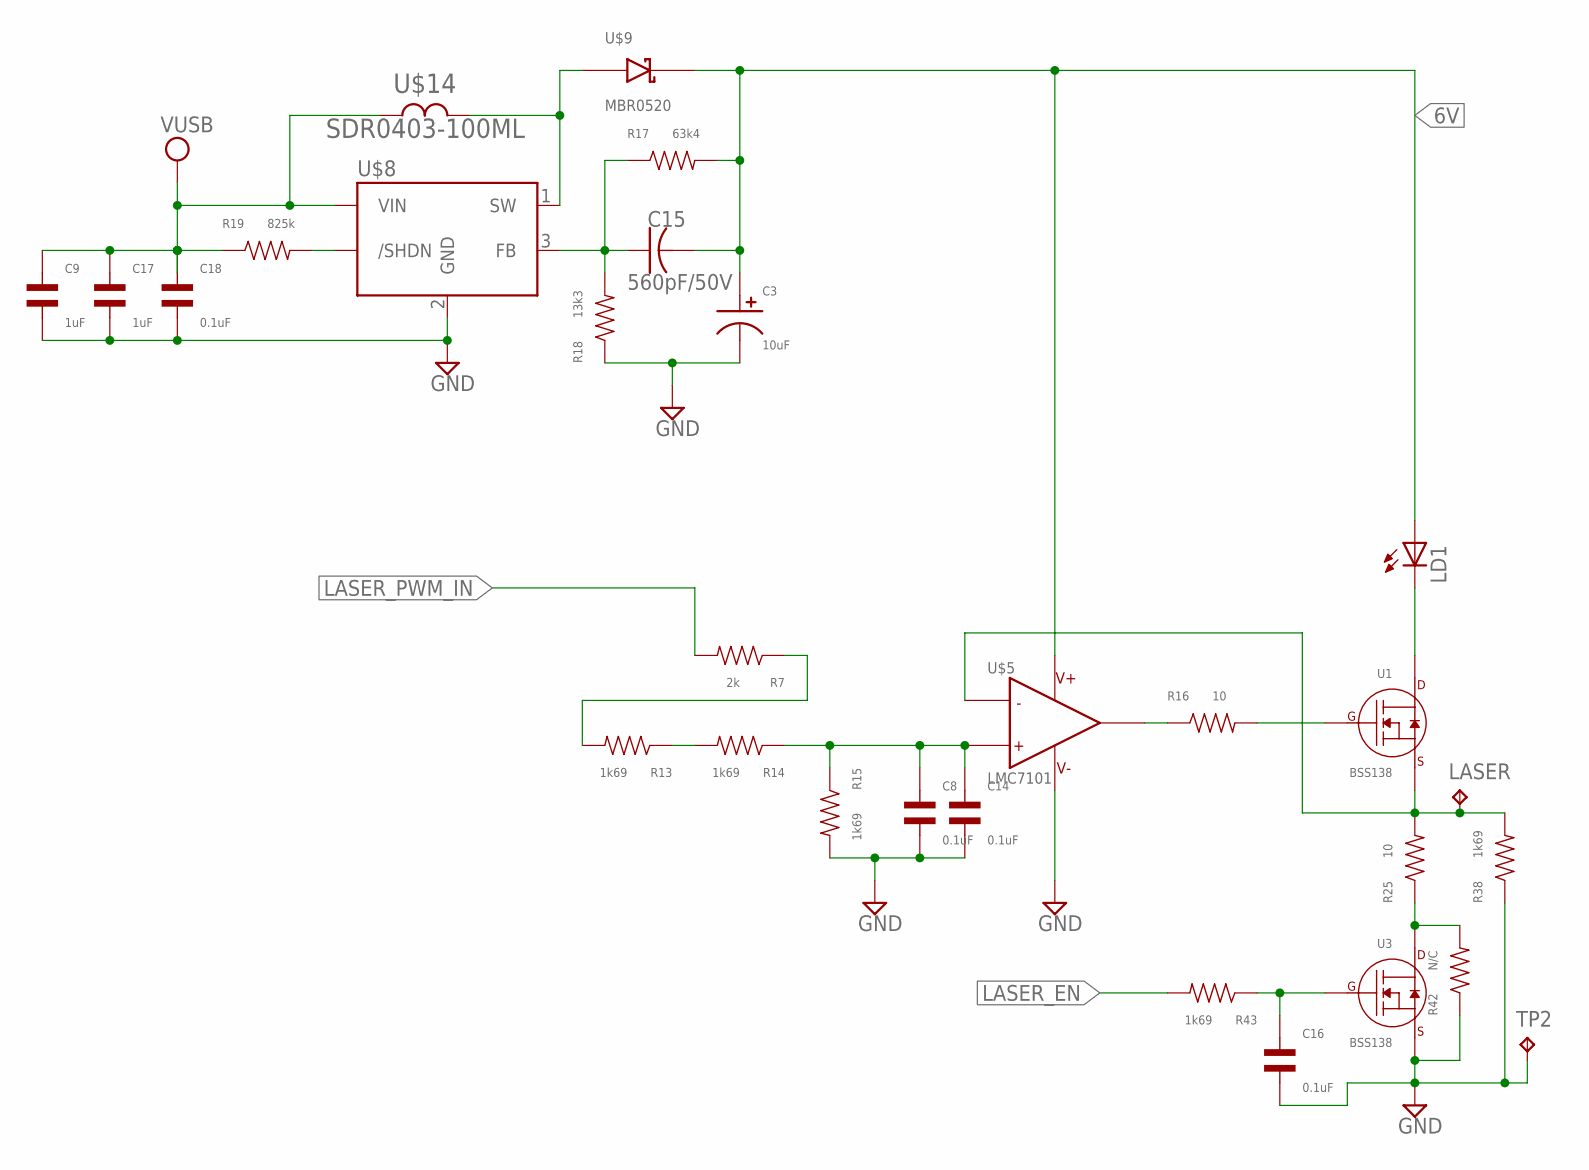
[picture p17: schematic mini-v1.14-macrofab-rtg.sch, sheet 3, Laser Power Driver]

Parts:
C3: 10uF; CP4MM
C8, C14, C16, C18: 0.1uF; C0603
C9, C17: 1uF; C0603
C15: 560pF/50V; C0603
LASER: TPB2,54; B2,54
LD1: SCOTT_LASERDIODELD3; SCOTT_LASERDIODE3; MPN 3 x (0552-2-15-15-11-27-10-0)
R7: 2k; R0603
R13, R14, R15, R38, R43: 1k69; R0603
R16, R25: 10; R0603
R17: 63k4; R0603
R18: 13k3; R0603
R19: 825k; R0603
R42: N/C; R0603
TP2: GND; B2,54
U1, U3: BSS138; SOT-23-3
U$5: LMC7101; SOT23-5
U$8: LMR62014; SOT23-5
U$9: MBR0520; SOD123
U$14: SDR0403-100ML; SDR0403

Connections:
6V: C3.P$1, C15.2, LD1.P$1 (A), R17.P$2, U$5.2 (V+), U$9.CATHODE
GND: C3.P$2, C8.P$2, C9.P$2, C14.P$2, C16.P$2, C17.P$2, C18.P$2, R15.P$2, R18.P$1, R38.P$1, R42.P$1, TP2.TP, U3.P$2 (SOURCE), U$5.5 (V-), U$8.2 (GND); also elsewhere on the board
LASER_EN: R43.P$2; also elsewhere on the board
LASER_PWM_IN: R7.P$2; also elsewhere on the board
unnamed: R25.P$1, R42.P$2, U3.P$3 (DRAIN)
unnamed: R7.P$1, R13.P$2
unnamed: R13.P$1, R14.P$2
unnamed: C8.P$1, C14.P$1, R14.P$1, R15.P$1, U$5.3 (IN+)
unnamed: U$8.1 (SW), U$9.ANODE, U$14.P$2
unnamed: LD1.P$3 (C), U1.P$3 (DRAIN)
unnamed: LASER.TP, R25.P$2, R38.P$2, U1.P$2 (SOURCE), U$5.4 (IN-)
unnamed: R16.P$2, U1.P$1 (GATE)
unnamed: R16.P$1, U$5.1 (OUT)
unnamed: C16.P$1, R43.P$1, U3.P$1 (GATE)
unnamed: C15.1, R17.P$1, R18.P$2, U$8.3 (FB)
unnamed: R19.P$2, U$8.4 (/SHDN)
VUSB: C9.P$1, C17.P$1, C18.P$1, R19.P$1, U$8.5 (VIN), U$14.P$1; also elsewhere on the board

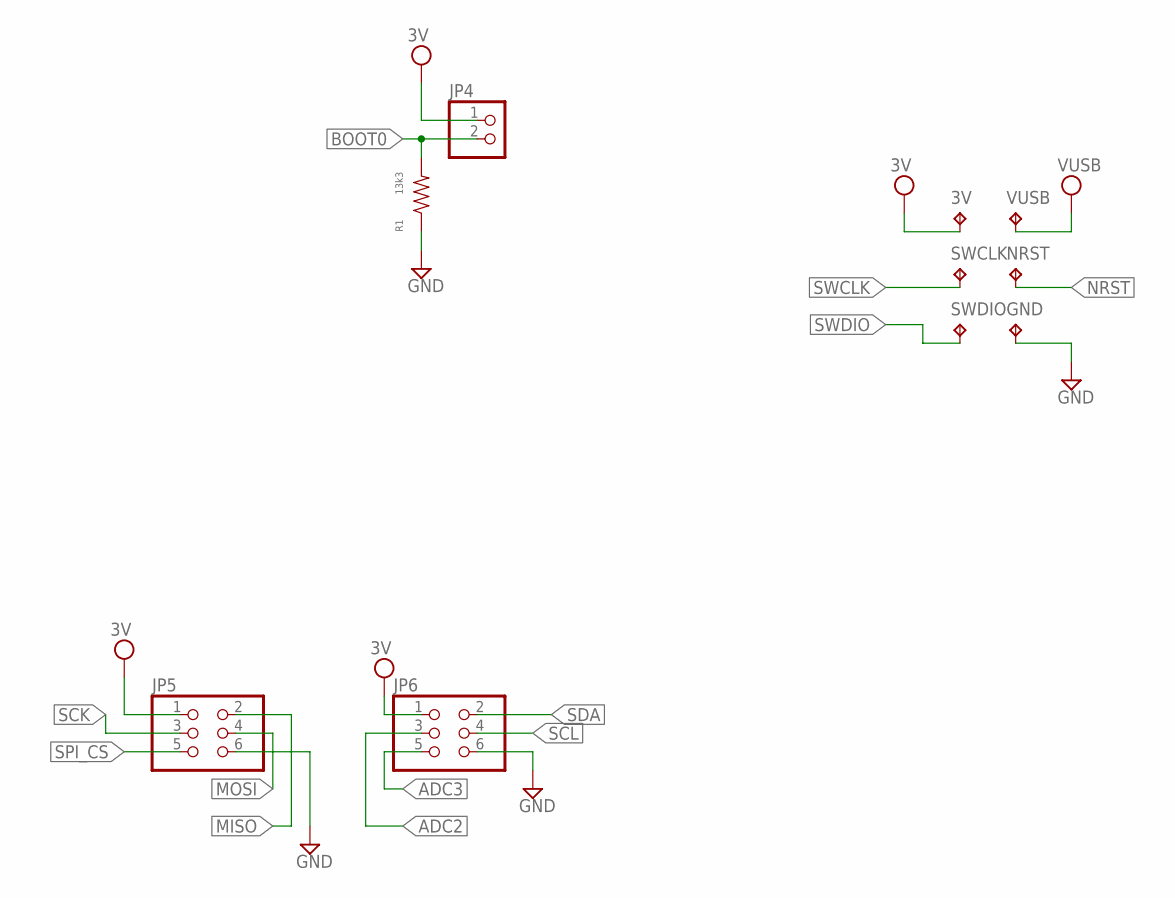
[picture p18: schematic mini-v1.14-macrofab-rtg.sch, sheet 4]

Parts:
3V: TPB1,27; B1,27
GND: TPB1,27; B1,27
JP4: PINHD-1X2; 1X02
JP5, JP6: PINHD-2X3; 2X03
NRST: TPB1,27; B1,27
R1: 13k3; R0603
SWCLK: TPB1,27; B1,27
SWDIO: TPB1,27; B1,27
VUSB: TPB1,27; B1,27

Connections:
3V: 3V.TP, JP4.1, JP5.1, JP6.1; also elsewhere on the board
ADC2: JP6.3; also elsewhere on the board
ADC3: JP6.5; also elsewhere on the board
BOOT0: JP4.2, R1.P$2; also elsewhere on the board
GND: GND.TP, JP5.6, JP6.6, R1.P$1; also elsewhere on the board
MISO: JP5.2; also elsewhere on the board
MOSI: JP5.4; also elsewhere on the board
NRST: NRST.TP; also elsewhere on the board
SCK: JP5.3; also elsewhere on the board
SCL: JP6.4; also elsewhere on the board
SDA: JP6.2; also elsewhere on the board
SPI_CS: JP5.5; also elsewhere on the board
SWCLK: SWCLK.TP; also elsewhere on the board
SWDIO: SWDIO.TP; also elsewhere on the board
VUSB: VUSB.TP; also elsewhere on the board

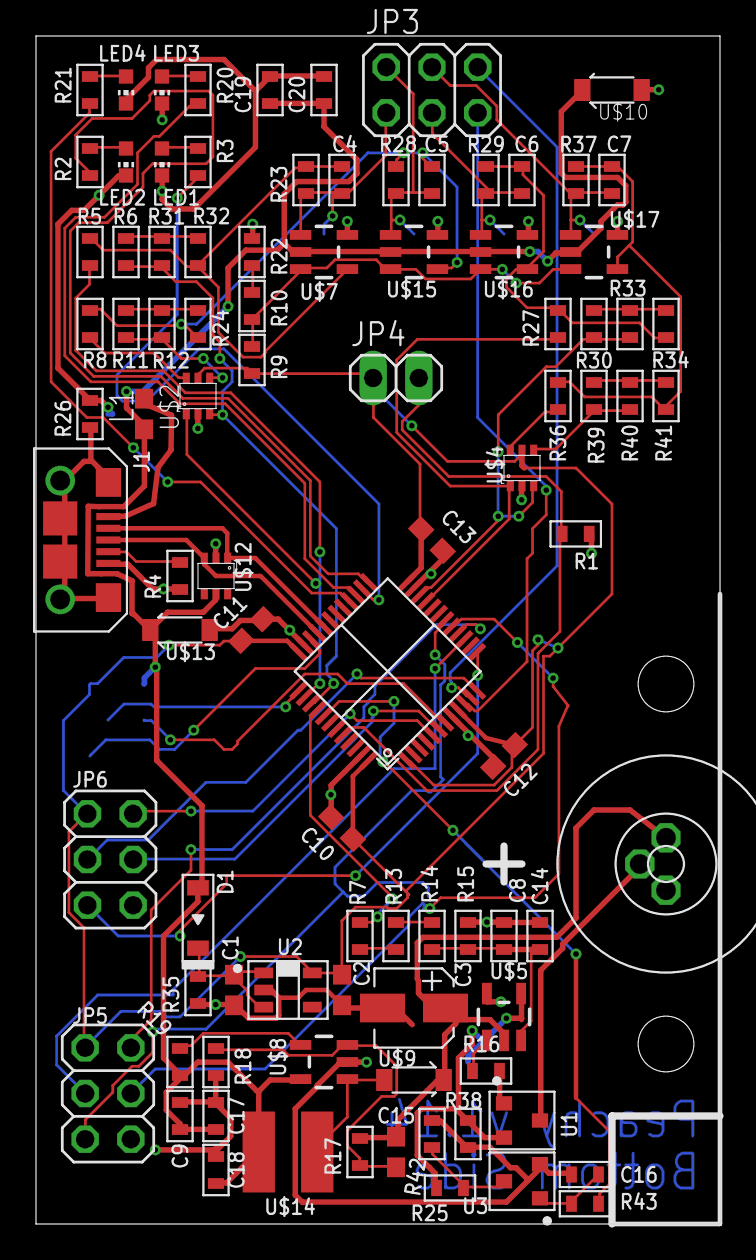
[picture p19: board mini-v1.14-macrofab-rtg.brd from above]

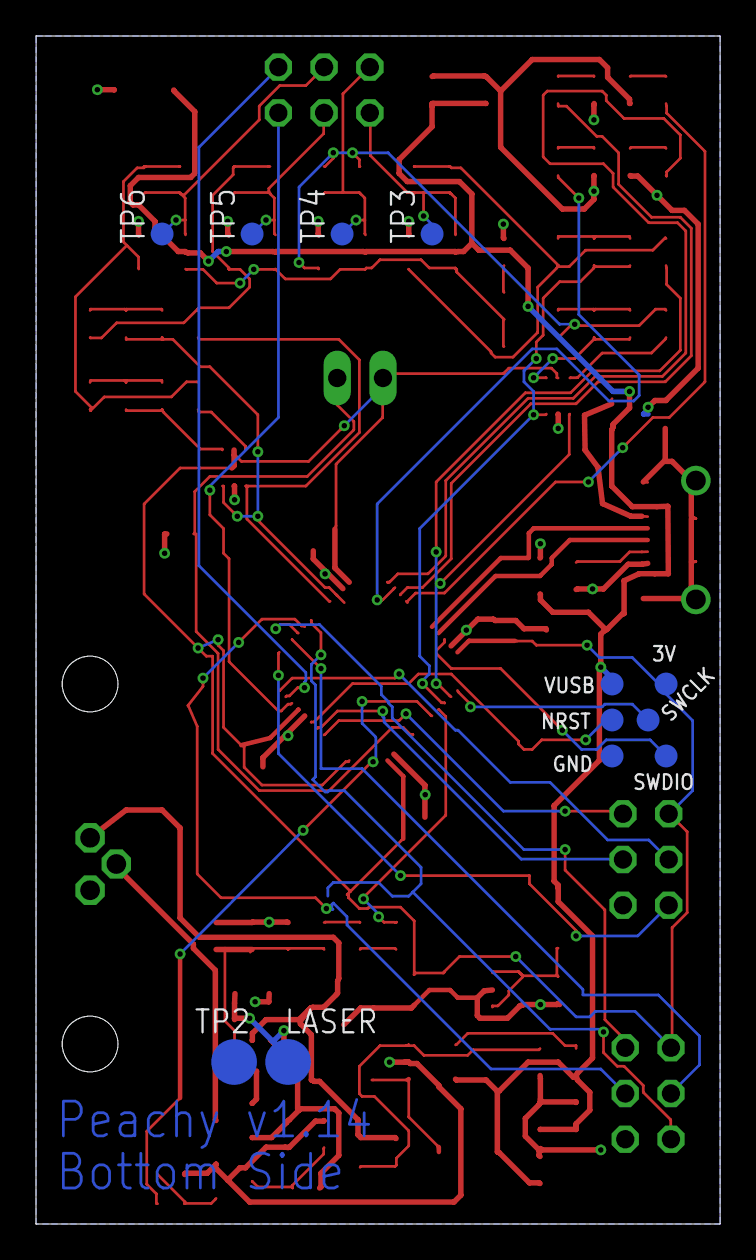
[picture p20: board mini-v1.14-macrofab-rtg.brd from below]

Board: 2 copper layers, 38.0 x 66.0 mm, 104 parts (12 on the bottom side), 68 nets.

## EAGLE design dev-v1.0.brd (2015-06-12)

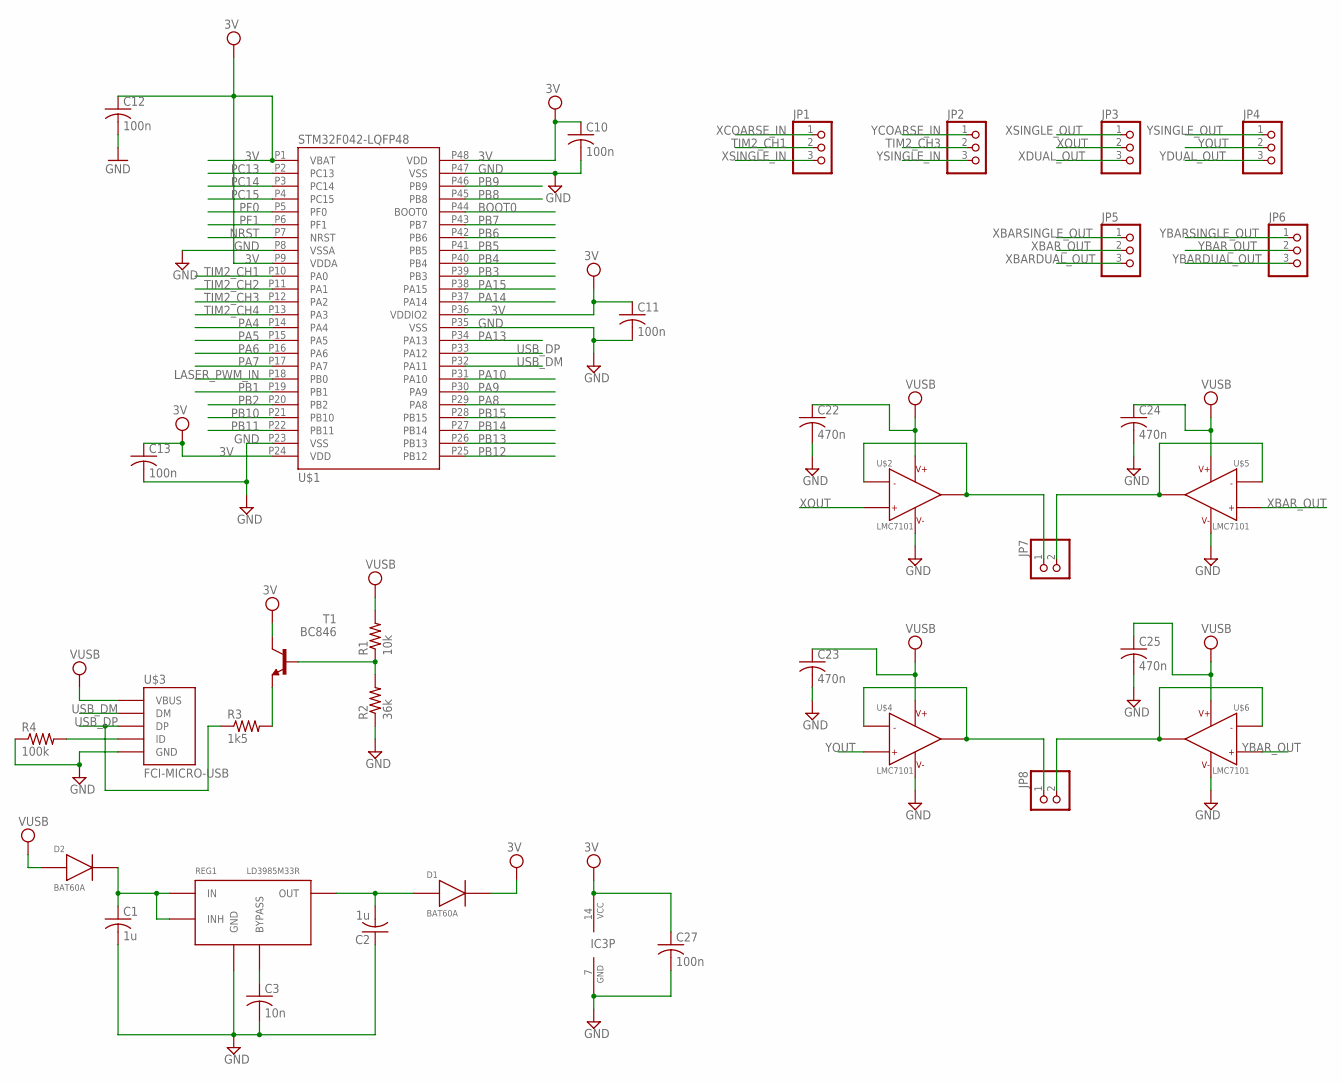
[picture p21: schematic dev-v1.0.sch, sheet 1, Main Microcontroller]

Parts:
C1, C2: 1u; C0603
C3: 10n; C0603
C10, C11, C12, C13, C27: 100n; C0603
C22, C23, C24, C25: 470n; C0603
D1, D2: BAT60A; SOD323
IC3: 74S04D; SO14
JP1, JP2, JP3, JP4, JP5, JP6: PINHD-1X3; 1X03
JP7, JP8: PINHD-1X2; 1X02
R1: 10k; R0603
R2: 36k; R0603
R3: 1k5; R0603
R4: 100k; R0603
REG1: LD3985M33R; SOT23-5L
T1: BC846; SOT23
U$1: STM32F042-LQFP48; LQFP48
U$2, U$4, U$5, U$6: LMC7101; SOT23-5
U$3: FCI-MICRO-USB; FCI-MICROUSB

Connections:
3V: C10.1, C11.1, C12.1, C13.1, C27.1, D1.1, IC3.14 (VCC), T1.3 (C), U$1.P1 (VBAT), U$1.P9 (VDDA), U$1.P24 (VDD), U$1.P36 (VDDIO2), U$1.P48 (VDD); also elsewhere on the board
3V3: C2.2, D1.2, REG1.OUT
BOOT0: U$1.P44 (BOOT0); also elsewhere on the board
GND: C1.2, C2.1, C3.2, C10.2, C11.2, C12.2, C13.2, C22.2, C23.2, C24.2, C25.2, C27.2, IC3.7 (GND), R2.1, R4.1, REG1.GND, U$1.P8 (VSSA), U$1.P23 (VSS), U$1.P35 (VSS), U$1.P47 (VSS), U$2.5, U$3.P5 (GND), U$4.5, U$5.5, U$6.5; also elsewhere on the board
LASER_PWM_IN: U$1.P18 (PB0); also elsewhere on the board
unnamed: C3.1, REG1.BYPASS
unnamed: R1.1, R2.2, T1.1 (B)
unnamed: R3.2, T1.2 (E)
unnamed: C1.1, D2.1, REG1.IN, REG1.INHIBIT (INH)
unnamed: R4.2, U$3.P4 (ID)
unnamed: JP7.1, U$2.1, U$2.4
unnamed: JP8.1, U$4.1, U$4.4
unnamed: JP7.2, U$5.1, U$5.4
unnamed: JP8.2, U$6.1, U$6.4
NRST: U$1.P7 (NRST); also elsewhere on the board
PA4: U$1.P14 (PA4); also elsewhere on the board
PA5: U$1.P15 (PA5); also elsewhere on the board
PA6: U$1.P16 (PA6); also elsewhere on the board
PA7: U$1.P17 (PA7); also elsewhere on the board
PA8: U$1.P29 (PA8); also elsewhere on the board
PA9: U$1.P30 (PA9); also elsewhere on the board
PA10: U$1.P31 (PA10); also elsewhere on the board
PA13: U$1.P34 (PA13); also elsewhere on the board
PA14: U$1.P37 (PA14); also elsewhere on the board
PA15: U$1.P38 (PA15); also elsewhere on the board
PB1: U$1.P19 (PB1); also elsewhere on the board
PB2: U$1.P20 (PB2); also elsewhere on the board
PB3: U$1.P39 (PB3); also elsewhere on the board
PB4: U$1.P40 (PB4); also elsewhere on the board
PB5: U$1.P41 (PB5); also elsewhere on the board
PB6: U$1.P42 (PB6); also elsewhere on the board
PB7: U$1.P43 (PB7); also elsewhere on the board
PB8: U$1.P45 (PB8); also elsewhere on the board
PB9: U$1.P46 (PB9); also elsewhere on the board
PB10: U$1.P21 (PB10); also elsewhere on the board
PB11: U$1.P22 (PB11); also elsewhere on the board
PB12: U$1.P25 (PB12); also elsewhere on the board
PB13: U$1.P26 (PB13); also elsewhere on the board
PB14: U$1.P27 (PB14); also elsewhere on the board
PB15: U$1.P28 (PB15); also elsewhere on the board
PC13: U$1.P2 (PC13); also elsewhere on the board
PC14: U$1.P3 (PC14); also elsewhere on the board
PC15: U$1.P4 (PC15); also elsewhere on the board
PF0: U$1.P5 (PF0); also elsewhere on the board
PF1: U$1.P6 (PF1); also elsewhere on the board
TIM2_CH1: JP1.2, U$1.P10 (PA0); also elsewhere on the board
TIM2_CH2: U$1.P11 (PA1); also elsewhere on the board
TIM2_CH3: JP2.2, U$1.P12 (PA2); also elsewhere on the board
TIM2_CH4: U$1.P13 (PA3); also elsewhere on the board
USB_DM: U$1.P32 (PA11), U$3.P2 (DM); also elsewhere on the board
USB_DP: R3.1, U$1.P33 (PA12), U$3.P3 (DP); also elsewhere on the board
VUSB: C22.1, C23.1, C24.1, C25.1, D2.2, R1.2, U$2.2, U$3.P1 (VBUS), U$4.2, U$5.2, U$6.2; also elsewhere on the board
XBARDUAL_OUT: JP5.3; also elsewhere on the board
XBARSINGLE_OUT: JP5.1; also elsewhere on the board
XBAR_OUT: JP5.2, U$5.3
XCOARSE_IN: JP1.1; also elsewhere on the board
XDUAL_OUT: JP3.3; also elsewhere on the board
XOUT: JP3.2, U$2.3
XSINGLE_IN: JP1.3; also elsewhere on the board
XSINGLE_OUT: JP3.1; also elsewhere on the board
YBARDUAL_OUT: JP6.3; also elsewhere on the board
YBARSINGLE_OUT: JP6.1; also elsewhere on the board
YBAR_OUT: JP6.2, U$6.3
YCOARSE_IN: JP2.1; also elsewhere on the board
YDUAL_OUT: JP4.3; also elsewhere on the board
YOUT: JP4.2, U$4.3
YSINGLE_IN: JP2.3; also elsewhere on the board
YSINGLE_OUT: JP4.1; also elsewhere on the board

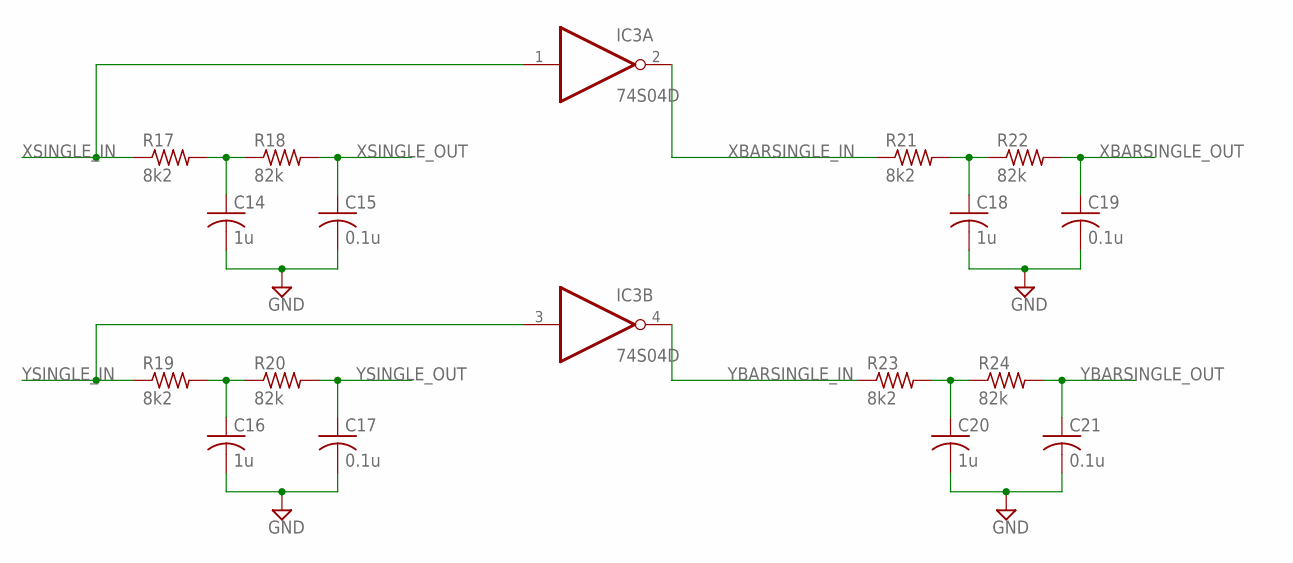
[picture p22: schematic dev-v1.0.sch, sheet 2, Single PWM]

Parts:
C14, C16, C18, C20: 1u; C0603
C15, C17, C19, C21: 0.1u; C0603
IC3: 74S04D; SO14
R17, R19, R21, R23: 8k2; R0603
R18, R20, R22, R24: 82k; R0603

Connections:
GND: C14.2, C15.2, C16.2, C17.2, C18.2, C19.2, C20.2, C21.2; also elsewhere on the board
unnamed: C14.1, R17.2, R18.1
unnamed: C16.1, R19.2, R20.1
unnamed: C18.1, R21.2, R22.1
unnamed: C20.1, R23.2, R24.1
XBARSINGLE_IN: IC3.2 (O), R21.1
XBARSINGLE_OUT: C19.1, R22.2; also elsewhere on the board
XSINGLE_IN: IC3.1 (I), R17.1; also elsewhere on the board
XSINGLE_OUT: C15.1, R18.2; also elsewhere on the board
YBARSINGLE_IN: IC3.4 (O), R23.1
YBARSINGLE_OUT: C21.1, R24.2; also elsewhere on the board
YSINGLE_IN: IC3.3 (I), R19.1; also elsewhere on the board
YSINGLE_OUT: C17.1, R20.2; also elsewhere on the board

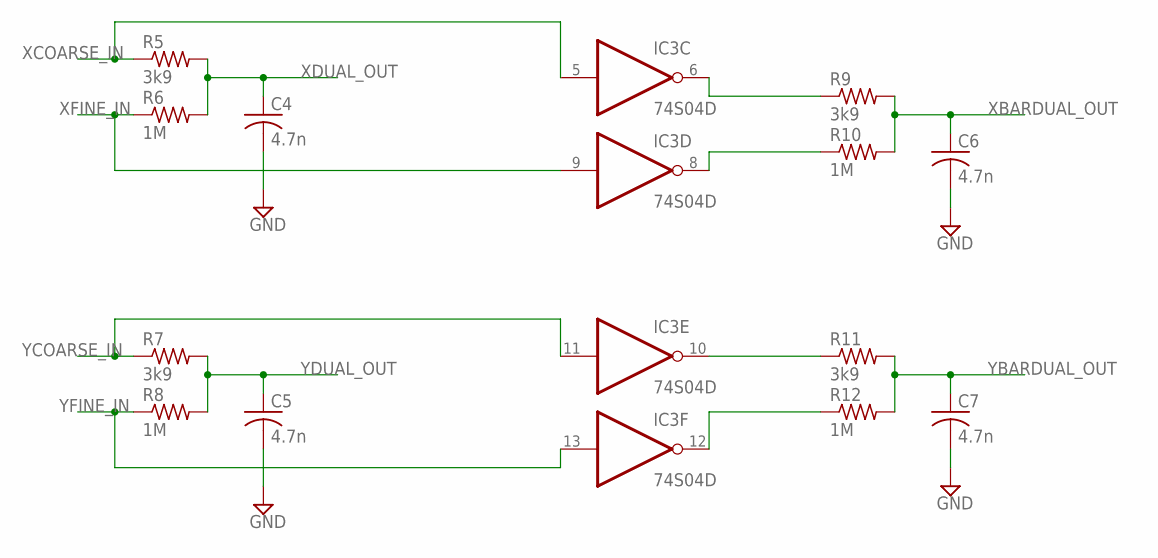
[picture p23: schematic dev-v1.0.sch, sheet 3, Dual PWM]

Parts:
C4, C5, C6, C7: 4.7n; C0603
IC3: 74S04D; SO14
R5, R7, R9, R11: 3k9; R0603
R6, R8, R10, R12: 1M; R0603

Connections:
GND: C4.2, C5.2, C6.2, C7.2; also elsewhere on the board
unnamed: IC3.10 (O), R11.1
unnamed: IC3.12 (O), R12.1
unnamed: IC3.8 (O), R10.1
unnamed: IC3.6 (O), R9.1
XBARDUAL_OUT: C6.1, R9.2, R10.2; also elsewhere on the board
XCOARSE_IN: IC3.5 (I), R5.1; also elsewhere on the board
XDUAL_OUT: C4.1, R5.2, R6.2; also elsewhere on the board
XFINE_IN: IC3.9 (I), R6.1
YBARDUAL_OUT: C7.1, R11.2, R12.2; also elsewhere on the board
YCOARSE_IN: IC3.11 (I), R7.1; also elsewhere on the board
YDUAL_OUT: C5.1, R7.2, R8.2; also elsewhere on the board
YFINE_IN: IC3.13 (I), R8.1

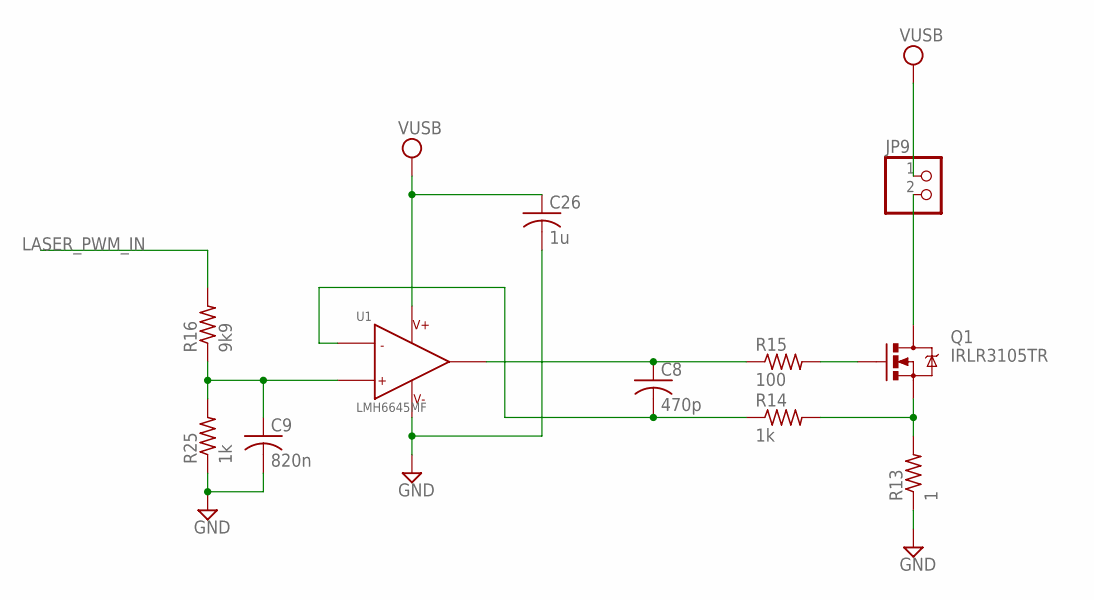
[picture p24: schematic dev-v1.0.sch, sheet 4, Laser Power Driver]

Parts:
C8: 470p; C0603
C9: 820n; C0603
C26: 1u; C0603
JP9: PINHD-1X2; 1X02
Q1: IRLR3105TR; DPAK
R13: 1; R0603
R14, R25: 1k; R0603
R15: 100; R0603
R16: 9k9; R0603
U1: LMH6645MF; SOT23-5

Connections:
GND: C9.2, C26.2, R13.1, R25.1, U1.2 (V-); also elsewhere on the board
LASER_PWM_IN: R16.2; also elsewhere on the board
unnamed: JP9.2, Q1.4 (D)
unnamed: Q1.3 (S), R13.2, R14.2
unnamed: C8.2, R14.1, U1.4 (IN-)
unnamed: Q1.1 (G), R15.2
unnamed: C8.1, R15.1, U1.1 (OUT)
unnamed: C9.1, R16.1, R25.2, U1.3 (IN+)
VUSB: C26.1, JP9.1, U1.5 (V+); also elsewhere on the board

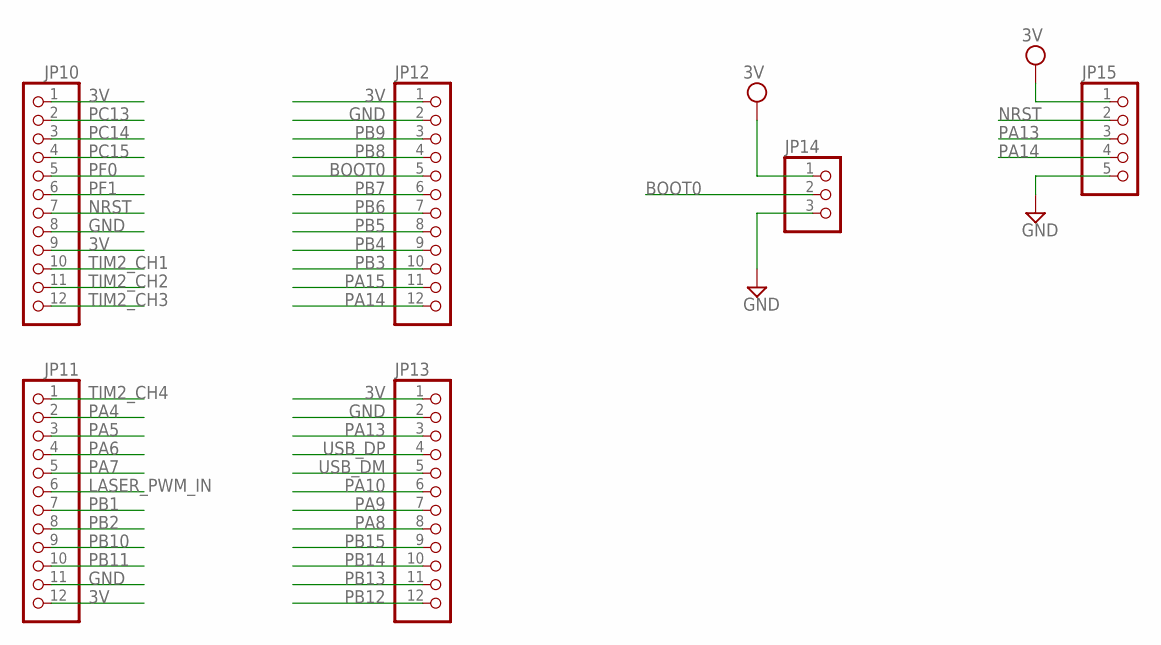
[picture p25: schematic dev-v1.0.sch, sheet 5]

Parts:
JP10, JP11, JP12, JP13: PINHD-1X12; 1X12
JP14: PINHD-1X3; 1X03
JP15: PINHD-1X5; 1X05

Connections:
3V: JP10.1, JP10.9, JP11.12, JP12.1, JP13.1, JP14.1, JP15.1; also elsewhere on the board
BOOT0: JP12.5, JP14.2; also elsewhere on the board
GND: JP10.8, JP11.11, JP12.2, JP13.2, JP14.3, JP15.5; also elsewhere on the board
LASER_PWM_IN: JP11.6; also elsewhere on the board
NRST: JP10.7, JP15.2; also elsewhere on the board
PA4: JP11.2; also elsewhere on the board
PA5: JP11.3; also elsewhere on the board
PA6: JP11.4; also elsewhere on the board
PA7: JP11.5; also elsewhere on the board
PA8: JP13.8; also elsewhere on the board
PA9: JP13.7; also elsewhere on the board
PA10: JP13.6; also elsewhere on the board
PA13: JP13.3, JP15.3; also elsewhere on the board
PA14: JP12.12, JP15.4; also elsewhere on the board
PA15: JP12.11; also elsewhere on the board
PB1: JP11.7; also elsewhere on the board
PB2: JP11.8; also elsewhere on the board
PB3: JP12.10; also elsewhere on the board
PB4: JP12.9; also elsewhere on the board
PB5: JP12.8; also elsewhere on the board
PB6: JP12.7; also elsewhere on the board
PB7: JP12.6; also elsewhere on the board
PB8: JP12.4; also elsewhere on the board
PB9: JP12.3; also elsewhere on the board
PB10: JP11.9; also elsewhere on the board
PB11: JP11.10; also elsewhere on the board
PB12: JP13.12; also elsewhere on the board
PB13: JP13.11; also elsewhere on the board
PB14: JP13.10; also elsewhere on the board
PB15: JP13.9; also elsewhere on the board
PC13: JP10.2; also elsewhere on the board
PC14: JP10.3; also elsewhere on the board
PC15: JP10.4; also elsewhere on the board
PF0: JP10.5; also elsewhere on the board
PF1: JP10.6; also elsewhere on the board
TIM2_CH1: JP10.10; also elsewhere on the board
TIM2_CH2: JP10.11; also elsewhere on the board
TIM2_CH3: JP10.12; also elsewhere on the board
TIM2_CH4: JP11.1; also elsewhere on the board
USB_DM: JP13.5; also elsewhere on the board
USB_DP: JP13.4; also elsewhere on the board

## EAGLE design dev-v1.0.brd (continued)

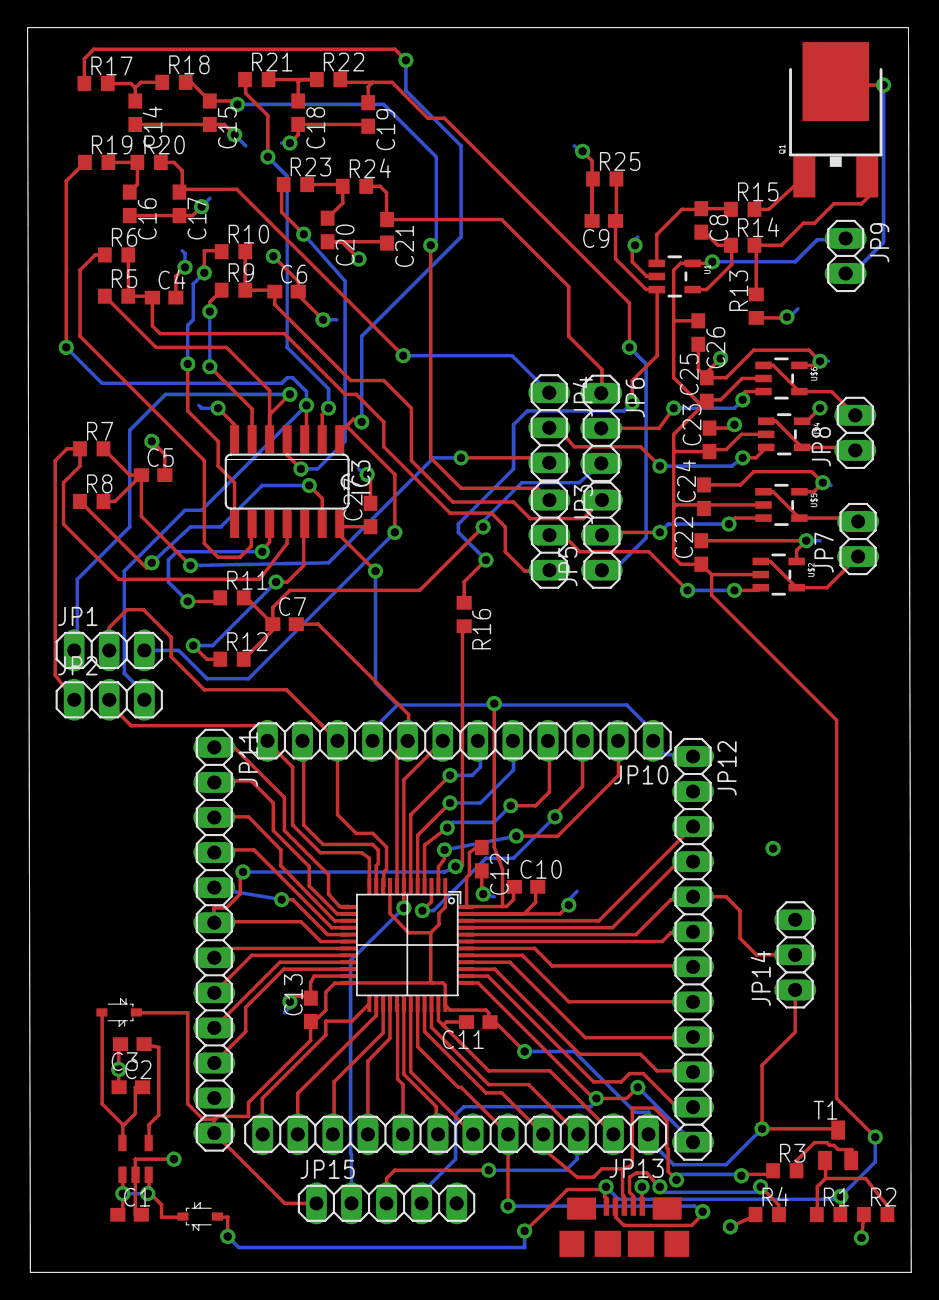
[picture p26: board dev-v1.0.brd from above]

Board: 2 copper layers, 64.0 x 90.2 mm, 80 parts (0 on the bottom side), 86 nets.

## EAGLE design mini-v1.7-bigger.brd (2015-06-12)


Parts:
C1, C2: 1u; C0603
C3: 10n; C0603
C10, C11, C12, C13, C27: 100n; C0603
C22, C23, C24, C25: 470n; C0603
D1, D2: BAT60A; SOD323
IC3: 74S04D; SO14
JP7, JP8: PINHD-1X2; 1X02
L1: ferrite; C0603
LED1, LED2, LED3, LED4: LEDCHIP-LED0603; CHIP-LED0603
R2, R3, R20, R21: R-US_R0603; R0603
R4: 100k; R0603
REG1: LD3985M33R; SOT23-5L
U$1: STM32F042-LQFP48; LQFP48
U$2, U$4, U$5, U$6: LMC7101; SOT23-5
U$3: FCI-MICRO-USB; FCI-MICROUSB
U$10, U$13: MBR0520; SOD123
U$11, U$12: SP3002; SC70-6

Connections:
3V: C10.1, C11.1, C12.1, C13.1, C27.1, D1.1, IC3.14 (VCC), U$1.P1 (VBAT), U$1.P9 (VDDA), U$1.P24 (VDD), U$1.P36 (VDDIO2), U$1.P48 (VDD); also elsewhere on the board
3V3: C2.2, D1.2, REG1.OUT
ADC0: U$1.P10 (PA0); also elsewhere on the board
ADC1: U$1.P11 (PA1); also elsewhere on the board
ADC2: U$1.P12 (PA2); also elsewhere on the board
ADC3: U$1.P13 (PA3); also elsewhere on the board
BOOT0: U$1.P44 (BOOT0); also elsewhere on the board
GND: C1.2, C2.1, C3.2, C10.2, C11.2, C12.2, C13.2, C22.2, C23.2, C24.2, C25.2, C27.2, IC3.7 (GND), LED1.C, LED2.C, LED3.C, LED4.C, R4.1, REG1.GND, U$1.P8 (VSSA), U$1.P23 (VSS), U$1.P35 (VSS), U$1.P47 (VSS), U$2.5, U$3.P5 (GND), U$4.5, U$5.5, U$6.5, U$10.ANODE, U$11.P2 (GND), U$12.P2 (GND), U$13.ANODE; also elsewhere on the board
LASER_PWM_IN: U$1.P40 (PB4); also elsewhere on the board
MISO: U$1.P16 (PA6); also elsewhere on the board
MOSI: U$1.P17 (PA7); also elsewhere on the board
unnamed: C3.1, REG1.BYPASS
unnamed: R2.2, U$1.P25 (PB12)
unnamed: LED2.A, R2.1
unnamed: C1.1, D2.1, REG1.IN, REG1.INHIBIT (INH)
unnamed: R4.2, U$3.P4 (ID)
unnamed: JP7.1, U$2.1, U$2.4, U$11.P6 (IO4)
unnamed: JP8.1, U$4.1, U$4.4, U$11.P1 (IO1)
unnamed: LED1.A, R3.1
unnamed: R3.2, U$1.P26 (PB13)
unnamed: L1.2, U$3.P1 (VBUS)
unnamed: JP7.2, U$5.1, U$5.4, U$11.P4 (IO3)
unnamed: JP8.2, U$6.1, U$6.4, U$11.P3 (IO2)
unnamed: LED3.A, R20.1
unnamed: LED4.A, R21.1
unnamed: R20.2, U$1.P27 (PB14)
unnamed: R21.2, U$1.P28 (PB15)
NRST: U$1.P7 (NRST); also elsewhere on the board
SCK: U$1.P15 (PA5); also elsewhere on the board
SCL: U$1.P6 (PF1); also elsewhere on the board
SDA: U$1.P5 (PF0); also elsewhere on the board
SPI_CS: U$1.P18 (PB0); also elsewhere on the board
SWCLK: U$1.P37 (PA14); also elsewhere on the board
SWDIO: U$1.P34 (PA13); also elsewhere on the board
USB_DM: U$1.P32 (PA11), U$3.P2 (DM), U$12.P1 (IO1)
USB_DP: U$1.P33 (PA12), U$3.P3 (DP), U$12.P3 (IO2)
VUSB: C22.1, C23.1, C24.1, C25.1, D2.2, L1.1, U$2.2, U$4.2, U$5.2, U$6.2, U$10.CATHODE, U$11.P5 (VCC), U$12.P5 (VCC), U$13.CATHODE; also elsewhere on the board
XBARDUAL_OUT: U$5.3; also elsewhere on the board
XCOARSE_IN: U$1.P38 (PA15); also elsewhere on the board
XDUAL_OUT: U$2.3; also elsewhere on the board
XFINE_IN: U$1.P39 (PB3); also elsewhere on the board
YBARDUAL_OUT: U$6.3; also elsewhere on the board
YCOARSE_IN: U$1.P21 (PB10); also elsewhere on the board
YDUAL_OUT: U$4.3; also elsewhere on the board
YFINE_IN: U$1.P22 (PB11); also elsewhere on the board


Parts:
C4, C5, C6, C7: 4.7n; C0603
IC3: 74S04D; SO14
R5, R7, R9, R11: 3k9; R0603
R6, R8, R10, R12: 1M; R0603

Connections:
GND: C4.2, C5.2, C6.2, C7.2, IC3.1 (I), IC3.3 (I); also elsewhere on the board
unnamed: IC3.10 (O), R11.1
unnamed: IC3.12 (O), R12.1
unnamed: IC3.8 (O), R10.1
unnamed: IC3.6 (O), R9.1
XBARDUAL_OUT: C6.1, R9.2, R10.2; also elsewhere on the board
XCOARSE_IN: IC3.5 (I), R5.1; also elsewhere on the board
XDUAL_OUT: C4.1, R5.2, R6.2; also elsewhere on the board
XFINE_IN: IC3.9 (I), R6.1; also elsewhere on the board
YBARDUAL_OUT: C7.1, R11.2, R12.2; also elsewhere on the board
YCOARSE_IN: IC3.11 (I), R7.1; also elsewhere on the board
YDUAL_OUT: C5.1, R7.2, R8.2; also elsewhere on the board
YFINE_IN: IC3.13 (I), R8.1; also elsewhere on the board


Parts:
C8: 470p; C0603
C9: 820n; C0603
C14: 10uF; C0603
C15: 560pF/50V; C0603
C16: 2.2u; C0603
C26: 1u; C0603
LD1: LASERDIODELD2; LASERDIODE2; MPN 3 x (0552-2-15-15-11-27-10-0)
Q1: IRLR3105TR; DPAK
R13: 1; R0603
R14, R25: 1k; R0603
R15: 100; R0603
R16: 9k9; R0603
R17: 52k3; R0603
R18: 13k3; R0603
R19: 1M; R0603
U1: LMH6645MF; SOT23-5
U$8: LMR62014; SOT23-5
U$9: MBR0520; SOD123
U$14: SDR0403-100ML; SDR0403

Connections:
6V: C14.1, C15.2, C26.1, LD1.P$1 (A), R17.2, U1.5 (V+), U$9.CATHODE
GND: C9.2, C14.2, C16.2, C26.2, R13.1, R18.1, R25.1, U1.2 (V-), U$8.2 (GND); also elsewhere on the board
LASER_PWM_IN: R16.2; also elsewhere on the board
unnamed: U$8.1 (SW), U$9.ANODE, U$14.P$2
unnamed: LD1.P$3 (C), Q1.4 (D)
unnamed: Q1.3 (S), R13.2, R14.2
unnamed: C8.2, R14.1, U1.4 (IN-)
unnamed: Q1.1 (G), R15.2
unnamed: C8.1, R15.1, U1.1 (OUT)
unnamed: C9.1, R16.1, R25.2, U1.3 (IN+)
unnamed: C15.1, R17.1, R18.2, U$8.3 (FB)
unnamed: R19.2, U$8.4 (/SHDN)
VUSB: C16.1, R19.1, U$8.5 (VIN), U$14.P$1; also elsewhere on the board


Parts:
JP1: PINHD-2X8; 2X08
JP2: PINHD-2X2; 2X02
JP4: PINHD-1X2; 1X02
R1: 10k; R0603

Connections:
3V: JP1.1, JP1.2, JP4.1; also elsewhere on the board
ADC0: JP1.11; also elsewhere on the board
ADC1: JP1.13; also elsewhere on the board
ADC2: JP1.8; also elsewhere on the board
ADC3: JP1.10; also elsewhere on the board
BOOT0: JP4.2, R1.2; also elsewhere on the board
GND: JP1.12, JP1.14, JP1.15, JP1.16, JP2.4, R1.1; also elsewhere on the board
MISO: JP1.9; also elsewhere on the board
MOSI: JP1.7; also elsewhere on the board
NRST: JP2.1; also elsewhere on the board
SCK: JP1.5; also elsewhere on the board
SCL: JP1.4; also elsewhere on the board
SDA: JP1.6; also elsewhere on the board
SPI_CS: JP1.3; also elsewhere on the board
SWCLK: JP2.2; also elsewhere on the board
SWDIO: JP2.3; also elsewhere on the board


Board: 2 copper layers, 38.0 x 66.0 mm, 74 parts (0 on the bottom side), 59 nets.

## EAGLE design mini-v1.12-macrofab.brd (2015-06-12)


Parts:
C1, C2: 1u; C0603
C10, C11, C12, C13: 100n; C0603
D2: BAT42; SOD323
J1: USB_MICRO_RIGHT; MICROUSB-RIGHT
L1: ferrite; C0603
LED1, LED2, LED3, LED4: LEDCHIP-LED0603; CHIP-LED0603
R2, R3, R20, R21: 2k; R0603
R4: 100k; R0603
R26: 604k; R0603
R35: 825k; R0603
U2: TLV70233PDBVR; SOT-23-5
U$1: STM32F042-LQFP48; LQFP48
U$10, U$13: SMF6.0A; SOD123
U$12: SP3002; SC70-6

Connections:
3V: C2.2, C10.1, C11.1, C12.1, C13.1, U2.P$5 (VOUT), U$1.P1 (VBAT), U$1.P9 (VDDA), U$1.P24 (VDD), U$1.P36 (VDDIO2), U$1.P48 (VDD); also elsewhere on the board
ADC0: U$1.P10 (PA0); also elsewhere on the board
ADC1: U$1.P11 (PA1); also elsewhere on the board
ADC2: U$1.P12 (PA2); also elsewhere on the board
ADC3: U$1.P13 (PA3); also elsewhere on the board
BOOT0: U$1.P44 (BOOT0); also elsewhere on the board
GND: C1.2, C2.1, C10.2, C11.2, C12.2, C13.2, J1.5 (GND), LED1.C, LED2.C, LED3.C, LED4.C, R4.1, R26.P$2, R35.P$1, U2.P$2 (GND/ADJ), U$1.P8 (VSSA), U$1.P23 (VSS), U$1.P35 (VSS), U$1.P47 (VSS), U$10.ANODE, U$12.P2 (GND), U$13.ANODE; also elsewhere on the board
LASER_PWM_IN: U$1.P40 (PB4); also elsewhere on the board
MISO: U$1.P16 (PA6); also elsewhere on the board
MOSI: U$1.P17 (PA7); also elsewhere on the board
unnamed: R2.2, U$1.P25 (PB12)
unnamed: LED2.A, R2.1
unnamed: C1.1, D2.1, R35.P$2, U2.P$1 (VIN), U2.P$3 (EN)
unnamed: J1.4 (ID), R4.2
unnamed: LED1.A, R3.1
unnamed: R3.2, U$1.P26 (PB13)
unnamed: J1.1 (5V), L1.2
unnamed: J1.S1 (SLD), J1.S2 (SLD), J1.S3 (SLD), J1.S4 (SLD), J1.S5 (SLD), J1.S6 (SLD), R26.P$1
unnamed: LED3.A, R20.1
unnamed: LED4.A, R21.1
unnamed: R20.2, U$1.P27 (PB14)
unnamed: R21.2, U$1.P28 (PB15)
NRST: U$1.P7 (NRST); also elsewhere on the board
SCK: U$1.P15 (PA5); also elsewhere on the board
SCL: U$1.P6 (PF1); also elsewhere on the board
SDA: U$1.P5 (PF0); also elsewhere on the board
SPI_CS: U$1.P18 (PB0); also elsewhere on the board
SWCLK: U$1.P37 (PA14); also elsewhere on the board
SWDIO: U$1.P34 (PA13); also elsewhere on the board
USB_DM: J1.2 (D-), U$1.P32 (PA11), U$12.P1 (IO1)
USB_DP: J1.3 (D+), U$1.P33 (PA12), U$12.P3 (IO2)
VUSB: D2.2, L1.1, U$10.CATHODE, U$12.P5 (VCC), U$13.CATHODE; also elsewhere on the board
XCOARSE_IN: U$1.P38 (PA15); also elsewhere on the board
XFINE_IN: U$1.P39 (PB3); also elsewhere on the board
YCOARSE_IN: U$1.P21 (PB10); also elsewhere on the board
YFINE_IN: U$1.P22 (PB11); also elsewhere on the board


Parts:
C4, C5, C6, C7: 1u; C0603
C19: 1uF; C0603
C20: 0.1uF; C0603
JP3: PINHD-2X3; 2X03
R5, R8, R9, R10, R22, R23, R27, R28, R29, R36, R37, R38: 2k; R0603
R6, R11, R12, R30, R31, R33, R39, R40: 825k; R0603
R24, R32, R34, R41: 604k; R0603
U$2, U$4: NC7WZ14P6X; SC70-6
U$7, U$15, U$16, U$17: LMC7101; SOT23-5

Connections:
3V: R9.2, R22.2, R28.2, R37.2, U$2.P5 (VCC), U$4.P5 (VCC); also elsewhere on the board
ADC0: JP3.5; also elsewhere on the board
ADC1: JP3.6; also elsewhere on the board
COARSE1: R8.1, U$2.P6 (Y1)
FINE1: R11.1, R12.1, U$2.P4 (Y2)
FINE3: R39.1, R40.1, U$4.P4 (Y2)
GND: C4.P$2, C5.P$2, C6.P$2, C7.P$2, C19.P$2, C20.P$2, R10.1, R23.1, R29.1, R38.1, U$2.P2 (GND), U$4.P2 (GND), U$7.5, U$15.5, U$16.5, U$17.5; also elsewhere on the board
unnamed: R36.1, U$4.P6 (Y1)
unnamed: R11.2, R12.2, R24.1
unnamed: C4.P$1, R8.2, R9.1, R10.2, R24.2, U$15.3
unnamed: R30.2, R33.2, R34.1
unnamed: R6.2, R31.2, R32.1
unnamed: C5.P$1, R27.2, R28.1, R29.2, R34.2, U$16.3
unnamed: R39.2, R40.2, R41.1
unnamed: C6.P$1, R36.2, R37.1, R38.2, R41.2, U$17.3
OUT: JP3.1, U$7.1, U$7.4
OUT1: JP3.2, U$15.1, U$15.4
OUT2: JP3.3, U$16.1, U$16.4
OUT3: JP3.4, U$17.1, U$17.4
VUSB: C19.P$1, C20.P$1, U$7.2, U$15.2, U$16.2, U$17.2; also elsewhere on the board
XCOARSE_IN: R5.1, U$2.P1 (A1); also elsewhere on the board
XFINE_IN: R6.1, R31.1, U$2.P3 (A2); also elsewhere on the board
XSUM: C7.P$1, R5.2, R22.1, R23.2, R32.2, U$7.3
YCOARSE_IN: R27.1, U$4.P1 (A1); also elsewhere on the board
YFINE_IN: R30.1, R33.1, U$4.P3 (A2); also elsewhere on the board


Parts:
C8, C18: 0.1u; C0603
C9, C17: 1u; C0603
C14: 10uF; C0603
C15: 560pF/50V; C0603
LD1: LASERDIODELD2; LASERDIODE2; MPN 3 x (0552-2-15-15-11-27-10-0)
R7: 2k; R0603
R13, R14, R15: 1k69; R0603
R16: 100; R0603
R17: 63k4; R0603
R18: 13k3; R0603
R19: 825k; R0603
R25: 10; R0603
U1: N-CHANNEL_FET_SOT-23-3; SOT-23-3
U$5: OPAMP-SINGLELMC7101; SOT23-5
U$8: LMR62014; SOT23-5
U$9: MBR0520; SOD123
U$14: SDR0403-100ML; SDR0403

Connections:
6V: C14.1, C15.2, LD1.P$1 (A), R17.2, U$5.2 (V+), U$9.CATHODE
GND: C8.P$2, C9.P$2, C14.2, C17.P$2, C18.P$2, R15.P$2, R18.1, R25.P$1, U$5.5 (V-), U$8.2 (GND); also elsewhere on the board
LASER_PWM_IN: R7.P$2; also elsewhere on the board
unnamed: R7.P$1, R13.P$2
unnamed: R13.P$1, R14.P$2
unnamed: C8.P$1, R14.P$1, R15.P$1, U$5.3 (IN+)
unnamed: U$8.1 (SW), U$9.ANODE, U$14.P$2
unnamed: LD1.P$3 (C), U1.P$3 (DRAIN)
unnamed: R25.P$2, U1.P$2 (SOURCE), U$5.4 (IN-)
unnamed: R16.P$2, U1.P$1 (GATE)
unnamed: R16.P$1, U$5.1 (OUT)
unnamed: C15.1, R17.1, R18.2, U$8.3 (FB)
unnamed: R19.2, U$8.4 (/SHDN)
VUSB: C9.P$1, C17.P$1, C18.P$1, R19.1, U$8.5 (VIN), U$14.P$1; also elsewhere on the board


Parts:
JP1, JP5, JP6: PINHD-2X3; 2X03
JP4: PINHD-1X2; 1X02
R1: 10k; R0603

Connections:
3V: JP1.1, JP4.1, JP5.1, JP6.1; also elsewhere on the board
ADC2: JP6.3; also elsewhere on the board
ADC3: JP6.5; also elsewhere on the board
BOOT0: JP4.2, R1.2; also elsewhere on the board
GND: JP1.6, JP5.6, JP6.6, R1.1; also elsewhere on the board
MISO: JP5.2; also elsewhere on the board
MOSI: JP5.4; also elsewhere on the board
NRST: JP1.4; also elsewhere on the board
SCK: JP5.3; also elsewhere on the board
SCL: JP6.4; also elsewhere on the board
SDA: JP6.2; also elsewhere on the board
SPI_CS: JP5.5; also elsewhere on the board
SWCLK: JP1.3; also elsewhere on the board
SWDIO: JP1.5; also elsewhere on the board
VUSB: JP1.2; also elsewhere on the board


Board: 2 copper layers, 38.0 x 66.0 mm, 88 parts (0 on the bottom side), 63 nets.

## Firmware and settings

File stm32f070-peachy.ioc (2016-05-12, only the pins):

Mcu.UserName=STM32F070CBTx
PA0.Signal=ADC_IN0
PA1.Signal=ADC_IN1
PA11.Signal=USB_DM
PA12.Signal=USB_DP
PA13.Signal=SYS_SWDIO
PA14.Signal=SYS_SWCLK
PA2.Signal=ADC_IN2
PA3.Signal=ADC_IN3
PA4.GPIO_Label=SPI_CS
PA4.Signal=GPIO_Output
PA5.Signal=SPI1_SCK
PA6.Signal=SPI1_MISO
PA7.Signal=SPI1_MOSI
PB0.GPIO_Label=YCOARSE_IN
PB0.Signal=S_TIM3_CH3
PB1.GPIO_Label=YFINE_IN
PB1.Signal=S_TIM3_CH4
PB10.Signal=I2C2_SCL
PB11.Signal=I2C2_SDA
PB14.GPIO_Label=LASER_PWM_IN
PB14.Signal=S_TIM15_CH1
PB15.GPIO_Label=LASER_EN
PB15.Signal=GPIO_Output
PB4.GPIO_Label=XCOARSE_IN
PB4.Signal=S_TIM3_CH1
PB5.GPIO_Label=XFINE_IN
PB5.Signal=S_TIM3_CH2
